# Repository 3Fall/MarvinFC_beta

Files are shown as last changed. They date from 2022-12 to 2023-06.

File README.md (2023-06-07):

# Marvin - the [soon] ultimate open-source rocket flight computer
### Suitable for middle to high power rockets.

>  - Hey, let's take whatever's left of our energy to live, and jam it into another flight computer, 
but this time let's make it posh and fix all the issues of the previous designs.
>  - No.
>  - We can use some pogo pin connectors.
>  - Fine.

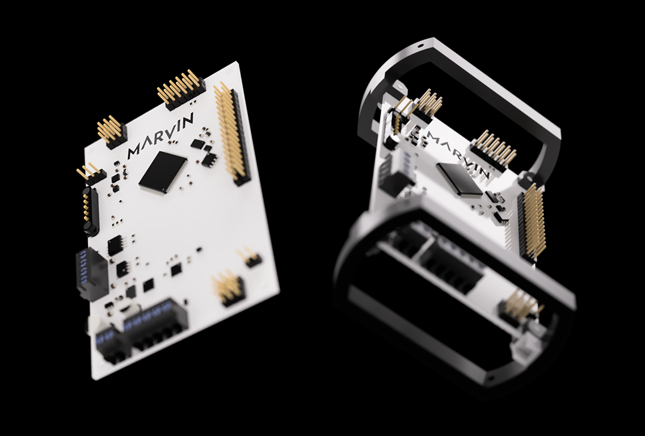
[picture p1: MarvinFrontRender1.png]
MarvinPic


# Specs:
- 65x100mm 1.6mm thick PCB
- 168Mhz STM32F407
- Separate power management chip ATTINY1607
- 3.3V, 5VPower, 5VExtension power buses
- Dual high current pyro channels with continuity detection circuitry
- 6 PWM outputs
- LSM6DSOTR IMU in sensor fusion configuration with LIS3MDLTR magnetometer
- MS5611 pressure sensor, barometric altitude and BMP280 as a redundancy or the budget friendly option
- Data logging to a 16Mbit flash memory chip and/or micro SD card
- 32 free GPIO
- Short time of black box data logging after an unexpected power outage 
- The coolest debug connector ever
- Default 433Mhz Ra-02 radio module (with proper antenna > 4km open space range easily achievable)
- Status and power indication LEDs

## Marvin is currently in testing phase, the schematics will likely change, but the development happens on our private server. Here, every version that gets put into production will be published.

# V2 Release:
- changed the magnetometer connection (now it's interfaced with the MCU directly)
- changed micro SD slot to one with visible pins
- fixed the lacking IMU I2C address pin connection (it was left floating in V1)
- the BMP280 pads were scaled up a bit, previously small enough to cause manufacturing problems with JLCPCB
- added power pins among the expansion pin deck
- added thermal relief to ground planes
- fixed the debug UART RX and TX labels
- added a buzzer
- added JST connectors for 3 of 6 PWM channels
- fixed the power management IC footprint
- changed the mounting holes to M3
- changed one of the LDO IC's to a different part

DevelopmentPic

Designed to fly a TVC rocket guided by artificial intelligence.
All the schematics and PCB files are available in the repo, but Marvin hasn't flown yet. Once it becomes flight proven, official version will be released.

# Software

```
The software is application specific, and thus not public.
```
Although below is the System Manager Firmware for the advanced power supply functionality.
> https://github.com/3Fall/Marvin_SystemManager_Firmware

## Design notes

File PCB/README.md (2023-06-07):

# marvin_v2

## TODO:

| What | Status | Notes
|---|---|---|
|Switch to 0805 footprints | ✅ | we too lazy |
|Magnetometer to mcu directly (no fusion config) | ✅ | done |
|AP622 swap | ✅ | we dont swap ig? |
|SD SLOT to one with visible pins | ✅ | done |
|IMU address pin | ✅ | done |
|Bigger bmp pads | ✅ | done |
|Voltage pins among PA and PE rows | ✅ | done |
|Sma for radio | ✅ | y tho |
| Add thermal relief to ground plane(s) | ✅ | DONE |
| Debug uart rx tx labels | ✅ | Switched around according to mcu docs |
|Buzzer | ✅ | added |
|Quick-plug connector | ✅ | added |
|Jst servo connectors | ✅ | added |
|PAC footprint | ✅ | switched |
|Mounting holes to m3 | ✅ | changed |
| U6 LDO swap | ✅ | chnged |

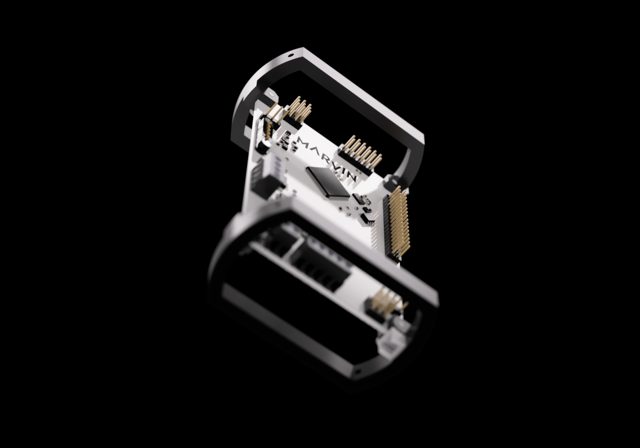
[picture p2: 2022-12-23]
Marvin1BackMount2.png

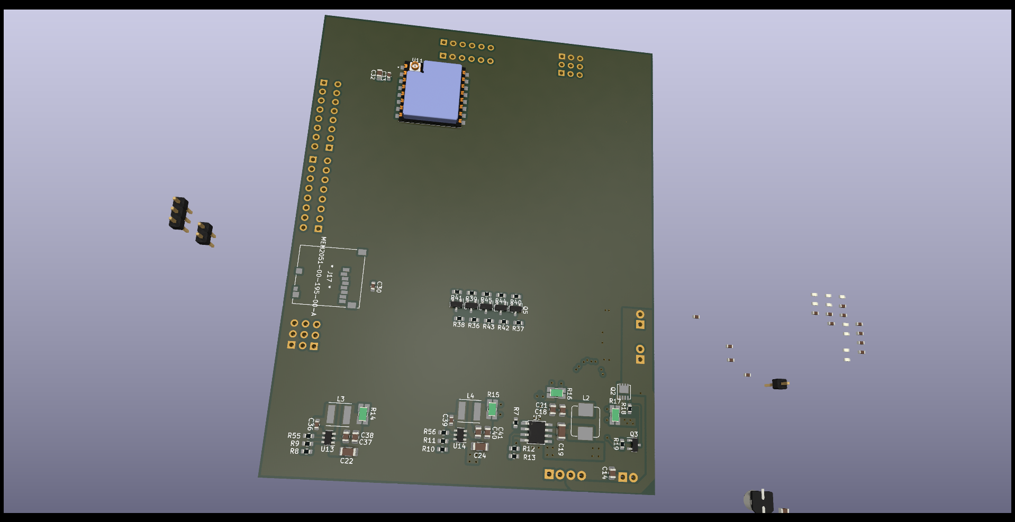
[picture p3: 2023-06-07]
PCB/marvin_fc_board.png

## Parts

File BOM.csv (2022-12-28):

Date: | 12/28/2022 5:08:15 PM
Tool: | Eeschema (6.0.10)
Component Count: | 160
Individual Components:
Item | Qty | Reference(s) | Value | LibPart | Footprint | Datasheet | MANUFACTURER | MAXIMUM_PACKAGE_HEIGHT | PARTREV | STANDARD
 |  | C1 | 20pF | Device:C_Small | Capacitor_SMD:C_0603_1608Metric | ~
 |  | C2 | 20pF | Device:C_Small | Capacitor_SMD:C_0603_1608Metric | ~
 |  | C3 | 100nF | Device:C_Small | Capacitor_SMD:C_0603_1608Metric | ~
 |  | C4 | 1uF | Device:C_Small | Capacitor_SMD:C_0603_1608Metric | ~
 |  | C5 | 2.2uF | Device:C_Small | Capacitor_SMD:C_0603_1608Metric | ~
 |  | C6 | 2.2uF | Device:C_Small | Capacitor_SMD:C_0603_1608Metric | ~
 |  | C7 | 1uF | Device:C_Small | Capacitor_SMD:C_0603_1608Metric | ~
 |  | C8 | 100nF | Device:C_Small | Capacitor_SMD:C_0603_1608Metric | ~
 |  | C9 | 100nF | Device:C_Small | Capacitor_SMD:C_0603_1608Metric | ~
 |  | C10 | 100nF | Device:C_Small | Capacitor_SMD:C_0603_1608Metric | ~
 |  | C11 | 1uF | Device:C_Small | Capacitor_SMD:C_0603_1608Metric | ~
 |  | C12 | 100nF | Device:C_Small | Capacitor_SMD:C_0603_1608Metric | ~
 |  | C13 | 100nF | Device:C_Small | Capacitor_SMD:C_0603_1608Metric | ~
 |  | C14 | 100nF | Device:C_Small | Capacitor_SMD:C_0603_1608Metric | ~
 |  | C15 | 100nF | Device:C_Small | Capacitor_SMD:C_0603_1608Metric | ~
 |  | C16 | 10u | Device:C | Capacitor_SMD:C_0805_2012Metric | ~
 |  | C17 | 10u | Device:C | Capacitor_SMD:C_0603_1608Metric | ~
 |  | C18 | 1000u | Device:C_Polarized | Capacitor_SMD:CP_Elec_6.3x7.7 | ~
 |  | C19 | 3300u | Device:C_Polarized | Capacitor_SMD:CP_Elec_5x5.4 | ~
 |  | C20 | 22u | Device:C | Capacitor_SMD:C_0805_2012Metric | ~
 |  | C21 | 10u | Device:C | Capacitor_SMD:C_1206_3216Metric | ~
 |  | C22 | 100n | Device:C | Capacitor_SMD:C_0603_1608Metric | ~
 |  | C23 | 22u | Device:C | Capacitor_SMD:C_0805_2012Metric | ~
 |  | C24 | 10u | Device:C | Capacitor_SMD:C_1206_3216Metric | ~
 |  | C25 | 100n | Device:C | Capacitor_SMD:C_0603_1608Metric | ~
 |  | C26 | 10u | Device:C | Capacitor_SMD:C_1206_3216Metric | ~
 |  | C27 | 100n | Device:C | Capacitor_SMD:C_0603_1608Metric | ~
 |  | C28 | 10u | Device:C | Capacitor_SMD:C_0805_2012Metric | ~
 |  | C29 | 100n | Device:C | Capacitor_SMD:C_0603_1608Metric | ~
 |  | C30 | 100n | Device:C | Capacitor_SMD:C_0603_1608Metric | ~
 |  | C31 | C | Device:C | Capacitor_SMD:C_0603_1608Metric | ~
 |  | C32 | 100n | Device:C | Capacitor_SMD:C_0603_1608Metric | ~
 |  | C33 | C | Device:C | Capacitor_SMD:C_0603_1608Metric | ~
 |  | C34 | 100nF | Device:C_Small | Capacitor_SMD:C_0603_1608Metric | ~
 |  | C35 | 100nF | Device:C_Small | Capacitor_SMD:C_0603_1608Metric | ~
 |  | C36 | 10u | Device:C | Capacitor_SMD:C_0805_2012Metric | ~
 |  | C37 | 100n | Device:C | Capacitor_SMD:C_0603_1608Metric | ~
 |  | C38 | 100u | Device:C | Capacitor_SMD:C_0805_2012Metric | ~
 |  | C39 | 100u | Device:C | Capacitor_SMD:C_0805_2012Metric | ~
 |  | C40 | 100n | Device:C_Small | Capacitor_SMD:C_0603_1608Metric | ~
 |  | C41 | 22u | Device:C | Capacitor_SMD:C_0805_2012Metric | ~
 |  | C42 | 22u | Device:C | Capacitor_SMD:C_0805_2012Metric | ~
 |  | C43 | 100n | Device:C_Small | Capacitor_SMD:C_0603_1608Metric | ~
 |  | C44 | 22u | Device:C | Capacitor_SMD:C_0805_2012Metric | ~
 |  | C45 | 22u | Device:C | Capacitor_SMD:C_0805_2012Metric | ~
 |  | D1 | LED_RGBK | Device:LED_RGBK | LED_SMD:LED_Cree-PLCC4_2x2mm_CW | ~
 |  | D2 | CUS08F30 | Device:D_Schottky | Diode_SMD:D_SOD-323_HandSoldering | ~
 |  | D3 | VBAT | Device:LED | LED_SMD:LED_0603_1608Metric_Pad1.05x0.95mm_HandSolder | ~
 |  | D4 | V5L | Device:LED | LED_SMD:LED_0603_1608Metric_Pad1.05x0.95mm_HandSolder | ~
 |  | D5 | V5P | Device:LED | LED_SMD:LED_0603_1608Metric_Pad1.05x0.95mm_HandSolder | ~
 |  | D6 | 3V3 | Device:LED | LED_SMD:LED_0603_1608Metric_Pad1.05x0.95mm_HandSolder | ~
 |  | D7 | LED_RGBK | Device:LED_RGBK | LED_SMD:LED_Cree-PLCC4_2x2mm_CW | ~
 |  | F1 | 200mA | Device:Polyfuse_Small | Fuse:Fuse_0603_1608Metric | ~
 |  | F2 | 200mA | Device:Polyfuse_Small | Fuse:Fuse_0603_1608Metric | ~
 |  | FB1 | FerriteBead | Device:FerriteBead | Inductor_SMD:L_0805_2012Metric | ~
 |  | FB2 | FerriteBead | Device:FerriteBead | Inductor_SMD:L_0805_2012Metric | ~
 |  | J1 | PROG / DBG | Connector_Generic:Conn_01x06 | Connector_PinHeader_2.54mm:PinHeader_1x06_P2.54mm_Vertical | ~
 |  | J2 | EXPA | Connector_Generic:Conn_01x08 | Connector_PinHeader_2.54mm:PinHeader_1x08_P2.54mm_Vertical | ~
 |  | J3 | EXPC | Connector_Generic:Conn_01x08 | Connector_PinHeader_2.54mm:PinHeader_1x08_P2.54mm_Vertical | ~
 |  | J4 | SERVO POW 1 | Connector_Generic:Conn_02x03_Odd_Even | Connector_PinHeader_2.54mm:PinHeader_2x03_P2.54mm_Vertical | ~
 |  | J5 | SERVO POW 2 | Connector_Generic:Conn_02x03_Odd_Even | Connector_PinHeader_2.54mm:PinHeader_2x03_P2.54mm_Vertical | ~
 |  | J6 | EXPB | Connector_Generic:Conn_01x08 | Connector_PinHeader_2.54mm:PinHeader_1x08_P2.54mm_Vertical | ~
 |  | J7 | EXPD | Connector_Generic:Conn_01x08 | Connector_PinHeader_2.54mm:PinHeader_1x08_P2.54mm_Vertical | ~
 |  | J8 | SERVO SIG 1 | Connector_Generic:Conn_01x03 | Connector_PinHeader_2.54mm:PinHeader_1x03_P2.54mm_Vertical | ~
 |  | J9 | SERVO SIG 2 | Connector_Generic:Conn_01x03 | Connector_PinHeader_2.54mm:PinHeader_1x03_P2.54mm_Vertical | ~
 |  | J10 | EXP1 | Connector_Generic:Conn_01x06 | Connector_PinHeader_2.54mm:PinHeader_1x06_P2.54mm_Vertical | ~
 |  | J11 | EXP2 | Connector_Generic:Conn_01x06 | Connector_PinHeader_2.54mm:PinHeader_1x06_P2.54mm_Vertical | ~
 |  | J12 | POWER_IN | Connector:Screw_Terminal_01x02 | TerminalBlock_4Ucon:TerminalBlock_4Ucon_1x02_P3.50mm_Vertical | ~
 |  | J13 | EXTl NTC | Connector_Generic:Conn_01x02 | Connector_PinHeader_2.54mm:PinHeader_1x02_P2.54mm_Vertical | ~
 |  | J14 | Screw_Terminal_01x05 | Connector:Screw_Terminal_01x05 | TerminalBlock_4Ucon:TerminalBlock_4Ucon_1x05_P3.50mm_Vertical | ~
 |  | J15 | ATTINY_DBG | Connector_Generic:Conn_01x03 | Connector_PinHeader_2.54mm:PinHeader_1x03_P2.54mm_Vertical | ~
 |  | J16 | MEM2051-00-195-00-A | MEM:MEM2051-00-195-00-A | SD:MEM2051-00-195-00-A
 |  | J17 | Pyro Terminal 1 | Connector:Screw_Terminal_01x02 | TerminalBlock_4Ucon:TerminalBlock_4Ucon_1x02_P3.50mm_Vertical | ~
 |  | J18 | Pyro Terminal 2 | Connector:Screw_Terminal_01x02 | TerminalBlock_4Ucon:TerminalBlock_4Ucon_1x02_P3.50mm_Vertical | ~
 |  | JP1 | SB_B | Jumper:SolderJumper_2_Bridged | Jumper:SolderJumper-2_P1.3mm_Bridged_Pad1.0x1.5mm | ~
 |  | JP2 | SB_B | Jumper:SolderJumper_2_Bridged | Jumper:SolderJumper-2_P1.3mm_Bridged_Pad1.0x1.5mm | ~
 |  | JP3 | SB C | Jumper:SolderJumper_2_Bridged | Jumper:SolderJumper-2_P1.3mm_Bridged_Pad1.0x1.5mm | ~
 |  | JP4 | SB O | Jumper:SolderJumper_2_Open | Jumper:SolderJumper-2_P1.3mm_Open_Pad1.0x1.5mm | ~
 |  | JP5 | SB O | Jumper:SolderJumper_2_Open | Jumper:SolderJumper-2_P1.3mm_Open_Pad1.0x1.5mm | ~
 |  | JP6 | SB C | Jumper:SolderJumper_2_Bridged | Jumper:SolderJumper-2_P1.3mm_Bridged_Pad1.0x1.5mm | ~
 |  | JP7 | SB O | Jumper:SolderJumper_2_Open | Jumper:SolderJumper-2_P1.3mm_Open_Pad1.0x1.5mm | ~
 |  | L1 | L_Ferrite | Device:L_Ferrite | Inductor_SMD:L_0805_2012Metric | ~
 |  | L2 | 3u3 | Device:L_Ferrite | Inductor_SMD:L_Bourns_SRP7028A_7.3x6.6mm | ~
 |  | L3 | 4,7u | Device:L_Ferrite | Inductor_SMD:L_Taiyo-Yuden_NR-50xx | ~
 |  | L4 | 4,7u | Device:L_Ferrite | Inductor_SMD:L_Taiyo-Yuden_NR-50xx | ~
 |  | Q1 | SISH101DN | Transistor_FET:SiS415DNT | Package_SO:Vishay_PowerPAK_1212-8_Single | https://www.vishay.com/docs/63684/sis415dnt.pdf
 |  | Q2 | SISH101DN | Transistor_FET:SiS415DNT | Package_SO:Vishay_PowerPAK_1212-8_Single | https://www.vishay.com/docs/63684/sis415dnt.pdf
 |  | Q3 | BC847 | Transistor_BJT:BC847 | Package_TO_SOT_SMD:SOT-23 | http://www.infineon.com/dgdl/Infineon-BC847SERIES_BC848SERIES_BC849SERIES_BC850SERIES-DS-v01_01-en.pdf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
 |  | Q4 | AO4822A | Transistor_FET:FDS6890A | Package_SO:SOIC-8_3.9x4.9mm_P1.27mm | https://www.onsemi.com/pub/Collateral/FDS6890A-D.PDF
 |  | R1 | 510ohm | Device:R | Resistor_SMD:R_0603_1608Metric | ~
 |  | R2 | 0 Ohm | Device:R | Resistor_SMD:R_0603_1608Metric | ~
 |  | R3 | NC | Device:R | Resistor_SMD:R_0603_1608Metric | ~
 |  | R4 | 46ohm | Device:R | Resistor_SMD:R_0603_1608Metric | ~
 |  | R5 | 330 | Device:R | Resistor_SMD:R_0603_1608Metric | ~
 |  | R6 | NC | Device:R | Resistor_SMD:R_0603_1608Metric | ~
 |  | R7 | NC | Device:R | Resistor_SMD:R_0603_1608Metric | ~
 |  | R8 | NC | Device:R | Resistor_SMD:R_0603_1608Metric | ~
 |  | R9 | 10k | Device:R | Resistor_SMD:R_0603_1608Metric | ~
 |  | R10 | 2137 | Device:R | Resistor_SMD:R_0603_1608Metric | ~
 |  | R11 | 42069 | Device:R | Resistor_SMD:R_0603_1608Metric | ~
 |  | R12 | ? | Device:R | Resistor_SMD:R_0603_1608Metric | ~
 |  | R13 | ? | Device:R | Resistor_SMD:R_0603_1608Metric | ~
 |  | R14 | 2137 | Device:R | Resistor_SMD:R_0603_1608Metric | ~
 |  | R15 | R | Device:R | Resistor_SMD:R_0603_1608Metric | ~
 |  | R16 | 0.05 | Device:R_Shunt | Resistor_SMD:R_Shunt_Ohmite_LVK12 | ~
 |  | R17 | 0.05 | Device:R_Shunt | Resistor_SMD:R_Shunt_Ohmite_LVK12 | ~
 |  | R18 | 0.01 | Device:R_Shunt | Resistor_SMD:R_Shunt_Ohmite_LVK12 | ~
 |  | R19 | 0.01 | Device:R_Shunt | Resistor_SMD:R_Shunt_Ohmite_LVK12 | ~
 |  | R20 | 10k | Device:R | Resistor_SMD:R_0603_1608Metric | ~
 |  | R21 | 10k | Device:R | Resistor_SMD:R_0603_1608Metric | ~
 |  | R22 | 10k | Device:R | Resistor_SMD:R_0603_1608Metric | ~
 |  | R23 | 4.7k | Device:R | Resistor_SMD:R_0603_1608Metric | ~
 |  | R24 | 10k | Device:R | Resistor_SMD:R_0603_1608Metric | ~
 |  | R25 | 10k | Device:R | Resistor_SMD:R_0603_1608Metric | ~
 |  | R26 | 2k | Device:R | Resistor_SMD:R_0603_1608Metric | ~
 |  | R27 | 500 | Device:R | Resistor_SMD:R_0603_1608Metric | ~
 |  | R28 | 2k | Device:R | Resistor_SMD:R_0603_1608Metric | ~
 |  | R29 | 500 | Device:R | Resistor_SMD:R_0603_1608Metric | ~
 |  | R30 | 500 | Device:R | Resistor_SMD:R_0603_1608Metric | ~
 |  | R31 | 500 | Device:R | Resistor_SMD:R_0603_1608Metric | ~
 |  | R32 | 300 | Device:R | Resistor_SMD:R_0603_1608Metric | ~
 |  | R33 | R | Device:R | Resistor_SMD:R_0603_1608Metric | ~
 |  | R34 | 2k | Device:R | Resistor_SMD:R_0603_1608Metric | ~
 |  | R35 | 2k | Device:R | Resistor_SMD:R_0603_1608Metric | ~
 |  | R36 | R | Device:R | Resistor_SMD:R_0603_1608Metric | ~
 |  | R37 | 2k | Device:R | Resistor_SMD:R_0603_1608Metric | ~
 |  | R38 | 2k | Device:R | Resistor_SMD:R_0603_1608Metric | ~
 |  | R39 | 10k | Device:R | Resistor_SMD:R_0603_1608Metric | ~
 |  | R40 | 370 | Device:R | Resistor_SMD:R_0603_1608Metric | ~
 |  | R41 | 1k | Device:R | Resistor_SMD:R_0603_1608Metric | ~
 |  | R42 | 10k | Device:R | Resistor_SMD:R_0603_1608Metric | ~
 |  | R43 | 370 | Device:R | Resistor_SMD:R_0603_1608Metric | ~
 |  | R44 | 1k | Device:R | Resistor_SMD:R_0603_1608Metric | ~
 |  | R45 | 10k | Device:R | Resistor_SMD:R_0603_1608Metric | ~
 |  | R46 | 10k | Device:R | Resistor_SMD:R_0603_1608Metric | ~
 |  | SW1 | SW_Push | Switch:SW_Push | FancySwitch:FancySwitchFootprint | ~
 |  | SW2 | SW_Push | Switch:SW_Push | FancySwitch:FancySwitchFootprint | ~
 |  | SW3 | SW_Push | Switch:SW_Push | FancySwitch:FancySwitchFootprint | ~
 |  | TP1 | 5V_BOOT | Connector:TestPoint | TestPoint:TestPoint_Pad_D1.5mm | ~
 |  | TP2 | VBUS | Connector:TestPoint | TestPoint:TestPoint_Pad_D1.5mm | ~
 |  | TP3 | VBAT | Connector:TestPoint | TestPoint:TestPoint_Pad_D1.5mm | ~
 |  | U1 | STM32F407 | MCU_ST_STM32F4:STM32F407VGTx | Package_QFP:LQFP-100_14x14mm_P0.5mm | http://www.st.com/st-web-ui/static/active/en/resource/technical/document/datasheet/DM00037051.pdf
 |  | U2 | BMP280 | Sensor_Pressure:BMP280 | Package_LGA:Bosch_LGA-8_2x2.5mm_P0.65mm_ClockwisePinNumbering | https://ae-bst.resource.bosch.com/media/_tech/media/datasheets/BST-BMP280-DS001.pdf
 |  | U3 | LSM6DSOTR | LSMDSO:LSM6DSOTR | Package_LGA:LGA-14_3x2.5mm_P0.5mm_LayoutBorder3x4y
 |  | U4 | LIS3MDLTR | LIS3:LIS3MDLTR | Package_LGA:LGA-12_2x2mm_P0.5mm
 |  | U5 | MS5611-01BA | Sensor_Pressure:MS5611-01BA | Package_LGA:LGA-8_3x5mm_P1.25mm | https://www.te.com/commerce/DocumentDelivery/DDEController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
 |  | U6 | NCP718xSN500 | Regulator_Linear:NCP718xSN500 | Package_TO_SOT_SMD:SOT-23-5 | https://www.onsemi.com/pub/Collateral/NCP718-D.PDF
 |  | U7 | ST1S41PHR | Regulator_Switching:ST1S10PHR | Package_SO:TI_SO-PowerPAD-8 | http://www.st.com/internet/com/TECHNICAL_RESOURCES/TECHNICAL_LITERATURE/DATASHEET/CD00169322.pdf
 |  | U8 | PAC1954 | Analog_ADC:PAC1934x-xJQ | Package_DFN_QFN:UQFN-16-1EP_4x4mm_P0.65mm_EP2.7x2.7mm | http://ww1.microchip.com/downloads/en/DeviceDoc/PAC1931-Family-Data-Sheet-DS20005850E.pdf
 |  | U9 | ATtiny1627-M | MCU_Microchip_ATtiny:ATtiny827-M | Package_DFN_QFN:QFN-24-1EP_4x4mm_P0.5mm_EP2.6x2.6mm | https://ww1.microchip.com/downloads/en/DeviceDoc/ATtiny424-426-427-824-826-827-DataSheet-DS40002311A.pdf
 |  | U10 | TXB0108DQSR | Logic_LevelTranslator:TXB0108DQSR | TXB0108:IC_TXB0108RGYR | http://www.ti.com/lit/ds/symlink/txb0108.pdf
 |  | U11 | W25Q16JLSSIG | W25Q:W25Q16JLSSIG | Package_SO:SOIC-8_3.9x4.9mm_P1.27mm
 |  | U12 | RA-02_LORA | RA 02:RA-02_LORA | LORA:MODULE_RA-02_LORA |  | Ai-Thinker | 3.3mm | 2018/03/02 | Manufacturer Recommendations
 |  | U13 | ILD213T | Isolator:LTV-827 | Package_SO:SO-8_5.3x6.2mm_P1.27mm | http://optoelectronics.liteon.com/upload/download/DS-70-96-0016/LTV-8X7%20series%20201610%20.pdf
 |  | U14 | AP62200Z6 | Regulator_Switching:AP62250Z6 | Package_SO:TSOP-6_1.65x3.05mm_P0.95mm | https://www.diodes.com/assets/Datasheets/AP62250.pdf
 |  | U15 | AP62200Z6 | Regulator_Switching:AP62250Z6 | Package_SO:TSOP-6_1.65x3.05mm_P0.95mm | https://www.diodes.com/assets/Datasheets/AP62250.pdf
 |  | U16 | MCP9700AT-ELT | Sensor_Temperature:MCP9700AT-ELT | Package_TO_SOT_SMD:SOT-353_SC-70-5 | http://ww1.microchip.com/downloads/en/DeviceDoc/20001942G.pdf
 |  | U17 | MCP9700AT-ELT | Sensor_Temperature:MCP9700AT-ELT | Package_TO_SOT_SMD:SOT-353_SC-70-5 | http://ww1.microchip.com/downloads/en/DeviceDoc/20001942G.pdf
 |  | U18 | MCP9700AT-ELT | Sensor_Temperature:MCP9700AT-ELT | Package_TO_SOT_SMD:SOT-353_SC-70-5 | http://ww1.microchip.com/downloads/en/DeviceDoc/20001942G.pdf
 |  | Y1 | Crystal_GND24 | Device:Crystal_GND24 | Oscillator:Oscillator_SMD_SeikoEpson_SG210-4Pin_2.5x2.0mm | ~
Collated Components:
Item | Qty | Reference(s) | Value | LibPart | Footprint | Datasheet | MANUFACTURER | MAXIMUM_PACKAGE_HEIGHT | PARTREV | STANDARD
1 | 2 | C1, C2 | 20pF | Device:C_Small | Capacitor_SMD:C_0603_1608Metric | ~
2 | 10 | C3, C8, C9, C10, C12, C13, C14, C15, C34, C35 | 100nF | Device:C_Small | Capacitor_SMD:C_0603_1608Metric | ~
3 | 3 | C4, C7, C11 | 1uF | Device:C_Small | Capacitor_SMD:C_0603_1608Metric | ~
4 | 2 | C5, C6 | 2.2uF | Device:C_Small | Capacitor_SMD:C_0603_1608Metric | ~
5 | 3 | C16, C28, C36 | 10u | Device:C | Capacitor_SMD:C_0805_2012Metric | ~
6 | 1 | C17 | 10u | Device:C | Capacitor_SMD:C_0603_1608Metric | ~
7 | 1 | C18 | 1000u | Device:C_Polarized | Capacitor_SMD:CP_Elec_6.3x7.7 | ~
8 | 1 | C19 | 3300u | Device:C_Polarized | Capacitor_SMD:CP_Elec_5x5.4 | ~
9 | 6 | C20, C23, C41, C42, C44, C45 | 22u | Device:C | Capacitor_SMD:C_0805_2012Metric | ~
10 | 3 | C21, C24, C26 | 10u | Device:C | Capacitor_SMD:C_1206_3216Metric | ~
11 | 7 | C22, C25, C27, C29, C30, C32, C37 | 100n | Device:C | Capacitor_SMD:C_0603_1608Metric | ~
12 | 2 | C31, C33 | C | Device:C | Capacitor_SMD:C_0603_1608Metric | ~
13 | 2 | C38, C39 | 100u | Device:C | Capacitor_SMD:C_0805_2012Metric | ~
14 | 2 | C40, C43 | 100n | Device:C_Small | Capacitor_SMD:C_0603_1608Metric | ~
15 | 2 | D1, D7 | LED_RGBK | Device:LED_RGBK | LED_SMD:LED_Cree-PLCC4_2x2mm_CW | ~
16 | 1 | D2 | CUS08F30 | Device:D_Schottky | Diode_SMD:D_SOD-323_HandSoldering | ~
17 | 1 | D3 | VBAT | Device:LED | LED_SMD:LED_0603_1608Metric_Pad1.05x0.95mm_HandSolder | ~
18 | 1 | D4 | V5L | Device:LED | LED_SMD:LED_0603_1608Metric_Pad1.05x0.95mm_HandSolder | ~
19 | 1 | D5 | V5P | Device:LED | LED_SMD:LED_0603_1608Metric_Pad1.05x0.95mm_HandSolder | ~
20 | 1 | D6 | 3V3 | Device:LED | LED_SMD:LED_0603_1608Metric_Pad1.05x0.95mm_HandSolder | ~
21 | 2 | F1, F2 | 200mA | Device:Polyfuse_Small | Fuse:Fuse_0603_1608Metric | ~
22 | 2 | FB1, FB2 | FerriteBead | Device:FerriteBead | Inductor_SMD:L_0805_2012Metric | ~
23 | 1 | J1 | PROG / DBG | Connector_Generic:Conn_01x06 | Connector_PinHeader_2.54mm:PinHeader_1x06_P2.54mm_Vertical | ~
24 | 1 | J2 | EXPA | Connector_Generic:Conn_01x08 | Connector_PinHeader_2.54mm:PinHeader_1x08_P2.54mm_Vertical | ~
25 | 1 | J3 | EXPC | Connector_Generic:Conn_01x08 | Connector_PinHeader_2.54mm:PinHeader_1x08_P2.54mm_Vertical | ~
26 | 1 | J4 | SERVO POW 1 | Connector_Generic:Conn_02x03_Odd_Even | Connector_PinHeader_2.54mm:PinHeader_2x03_P2.54mm_Vertical | ~
27 | 1 | J5 | SERVO POW 2 | Connector_Generic:Conn_02x03_Odd_Even | Connector_PinHeader_2.54mm:PinHeader_2x03_P2.54mm_Vertical | ~
28 | 1 | J6 | EXPB | Connector_Generic:Conn_01x08 | Connector_PinHeader_2.54mm:PinHeader_1x08_P2.54mm_Vertical | ~
29 | 1 | J7 | EXPD | Connector_Generic:Conn_01x08 | Connector_PinHeader_2.54mm:PinHeader_1x08_P2.54mm_Vertical | ~
30 | 1 | J8 | SERVO SIG 1 | Connector_Generic:Conn_01x03 | Connector_PinHeader_2.54mm:PinHeader_1x03_P2.54mm_Vertical | ~
31 | 1 | J9 | SERVO SIG 2 | Connector_Generic:Conn_01x03 | Connector_PinHeader_2.54mm:PinHeader_1x03_P2.54mm_Vertical | ~
32 | 1 | J10 | EXP1 | Connector_Generic:Conn_01x06 | Connector_PinHeader_2.54mm:PinHeader_1x06_P2.54mm_Vertical | ~
33 | 1 | J11 | EXP2 | Connector_Generic:Conn_01x06 | Connector_PinHeader_2.54mm:PinHeader_1x06_P2.54mm_Vertical | ~
34 | 1 | J12 | POWER_IN | Connector:Screw_Terminal_01x02 | TerminalBlock_4Ucon:TerminalBlock_4Ucon_1x02_P3.50mm_Vertical | ~
35 | 1 | J13 | EXTl NTC | Connector_Generic:Conn_01x02 | Connector_PinHeader_2.54mm:PinHeader_1x02_P2.54mm_Vertical | ~
36 | 1 | J14 | Screw_Terminal_01x05 | Connector:Screw_Terminal_01x05 | TerminalBlock_4Ucon:TerminalBlock_4Ucon_1x05_P3.50mm_Vertical | ~
37 | 1 | J15 | ATTINY_DBG | Connector_Generic:Conn_01x03 | Connector_PinHeader_2.54mm:PinHeader_1x03_P2.54mm_Vertical | ~
38 | 1 | J16 | MEM2051-00-195-00-A | MEM:MEM2051-00-195-00-A | SD:MEM2051-00-195-00-A
39 | 1 | J17 | Pyro Terminal 1 | Connector:Screw_Terminal_01x02 | TerminalBlock_4Ucon:TerminalBlock_4Ucon_1x02_P3.50mm_Vertical | ~
40 | 1 | J18 | Pyro Terminal 2 | Connector:Screw_Terminal_01x02 | TerminalBlock_4Ucon:TerminalBlock_4Ucon_1x02_P3.50mm_Vertical | ~
41 | 2 | JP1, JP2 | SB_B | Jumper:SolderJumper_2_Bridged | Jumper:SolderJumper-2_P1.3mm_Bridged_Pad1.0x1.5mm | ~
42 | 2 | JP3, JP6 | SB C | Jumper:SolderJumper_2_Bridged | Jumper:SolderJumper-2_P1.3mm_Bridged_Pad1.0x1.5mm | ~
43 | 3 | JP4, JP5, JP7 | SB O | Jumper:SolderJumper_2_Open | Jumper:SolderJumper-2_P1.3mm_Open_Pad1.0x1.5mm | ~
44 | 1 | L1 | L_Ferrite | Device:L_Ferrite | Inductor_SMD:L_0805_2012Metric | ~
45 | 1 | L2 | 3u3 | Device:L_Ferrite | Inductor_SMD:L_Bourns_SRP7028A_7.3x6.6mm | ~
46 | 2 | L3, L4 | 4,7u | Device:L_Ferrite | Inductor_SMD:L_Taiyo-Yuden_NR-50xx | ~
47 | 2 | Q1, Q2 | SISH101DN | Transistor_FET:SiS415DNT | Package_SO:Vishay_PowerPAK_1212-8_Single | https://www.vishay.com/docs/63684/sis415dnt.pdf
48 | 1 | Q3 | BC847 | Transistor_BJT:BC847 | Package_TO_SOT_SMD:SOT-23 | http://www.infineon.com/dgdl/Infineon-BC847SERIES_BC848SERIES_BC849SERIES_BC850SERIES-DS-v01_01-en.pdf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
49 | 1 | Q4 | AO4822A | Transistor_FET:FDS6890A | Package_SO:SOIC-8_3.9x4.9mm_P1.27mm | https://www.onsemi.com/pub/Collateral/FDS6890A-D.PDF
50 | 1 | R1 | 510ohm | Device:R | Resistor_SMD:R_0603_1608Metric | ~
51 | 1 | R2 | 0 Ohm | Device:R | Resistor_SMD:R_0603_1608Metric | ~
52 | 4 | R3, R6, R7, R8 | NC | Device:R | Resistor_SMD:R_0603_1608Metric | ~
53 | 1 | R4 | 46ohm | Device:R | Resistor_SMD:R_0603_1608Metric | ~
54 | 1 | R5 | 330 | Device:R | Resistor_SMD:R_0603_1608Metric | ~
55 | 10 | R9, R20, R21, R22, R24, R25, R39, R42, R45, R46 | 10k | Device:R | Resistor_SMD:R_0603_1608Metric | ~
56 | 2 | R10, R14 | 2137 | Device:R | Resistor_SMD:R_0603_1608Metric | ~
57 | 1 | R11 | 42069 | Device:R | Resistor_SMD:R_0603_1608Metric | ~
58 | 2 | R12, R13 | ? | Device:R | Resistor_SMD:R_0603_1608Metric | ~
59 | 3 | R15, R33, R36 | R | Device:R | Resistor_SMD:R_0603_1608Metric | ~
60 | 2 | R16, R17 | 0.05 | Device:R_Shunt | Resistor_SMD:R_Shunt_Ohmite_LVK12 | ~
61 | 2 | R18, R19 | 0.01 | Device:R_Shunt | Resistor_SMD:R_Shunt_Ohmite_LVK12 | ~
62 | 1 | R23 | 4.7k | Device:R | Resistor_SMD:R_0603_1608Metric | ~
63 | 6 | R26, R28, R34, R35, R37, R38 | 2k | Device:R | Resistor_SMD:R_0603_1608Metric | ~
64 | 4 | R27, R29, R30, R31 | 500 | Device:R | Resistor_SMD:R_0603_1608Metric | ~
65 | 1 | R32 | 300 | Device:R | Resistor_SMD:R_0603_1608Metric | ~
66 | 2 | R40, R43 | 370 | Device:R | Resistor_SMD:R_0603_1608Metric | ~
67 | 2 | R41, R44 | 1k | Device:R | Resistor_SMD:R_0603_1608Metric | ~
68 | 3 | SW1, SW2, SW3 | SW_Push | Switch:SW_Push | FancySwitch:FancySwitchFootprint | ~
69 | 1 | TP1 | 5V_BOOT | Connector:TestPoint | TestPoint:TestPoint_Pad_D1.5mm | ~
70 | 1 | TP2 | VBUS | Connector:TestPoint | TestPoint:TestPoint_Pad_D1.5mm | ~
71 | 1 | TP3 | VBAT | Connector:TestPoint | TestPoint:TestPoint_Pad_D1.5mm | ~
72 | 1 | U1 | STM32F407 | MCU_ST_STM32F4:STM32F407VGTx | Package_QFP:LQFP-100_14x14mm_P0.5mm | http://www.st.com/st-web-ui/static/active/en/resource/technical/document/datasheet/DM00037051.pdf
73 | 1 | U2 | BMP280 | Sensor_Pressure:BMP280 | Package_LGA:Bosch_LGA-8_2x2.5mm_P0.65mm_ClockwisePinNumbering | https://ae-bst.resource.bosch.com/media/_tech/media/datasheets/BST-BMP280-DS001.pdf
74 | 1 | U3 | LSM6DSOTR | LSMDSO:LSM6DSOTR | Package_LGA:LGA-14_3x2.5mm_P0.5mm_LayoutBorder3x4y
75 | 1 | U4 | LIS3MDLTR | LIS3:LIS3MDLTR | Package_LGA:LGA-12_2x2mm_P0.5mm
76 | 1 | U5 | MS5611-01BA | Sensor_Pressure:MS5611-01BA | Package_LGA:LGA-8_3x5mm_P1.25mm | https://www.te.com/commerce/DocumentDelivery/DDEController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
77 | 1 | U6 | NCP718xSN500 | Regulator_Linear:NCP718xSN500 | Package_TO_SOT_SMD:SOT-23-5 | https://www.onsemi.com/pub/Collateral/NCP718-D.PDF
78 | 1 | U7 | ST1S41PHR | Regulator_Switching:ST1S10PHR | Package_SO:TI_SO-PowerPAD-8 | http://www.st.com/internet/com/TECHNICAL_RESOURCES/TECHNICAL_LITERATURE/DATASHEET/CD00169322.pdf
79 | 1 | U8 | PAC1954 | Analog_ADC:PAC1934x-xJQ | Package_DFN_QFN:UQFN-16-1EP_4x4mm_P0.65mm_EP2.7x2.7mm | http://ww1.microchip.com/downloads/en/DeviceDoc/PAC1931-Family-Data-Sheet-DS20005850E.pdf
80 | 1 | U9 | ATtiny1627-M | MCU_Microchip_ATtiny:ATtiny827-M | Package_DFN_QFN:QFN-24-1EP_4x4mm_P0.5mm_EP2.6x2.6mm | https://ww1.microchip.com/downloads/en/DeviceDoc/ATtiny424-426-427-824-826-827-DataSheet-DS40002311A.pdf
81 | 1 | U10 | TXB0108DQSR | Logic_LevelTranslator:TXB0108DQSR | TXB0108:IC_TXB0108RGYR | http://www.ti.com/lit/ds/symlink/txb0108.pdf
82 | 1 | U11 | W25Q16JLSSIG | W25Q:W25Q16JLSSIG | Package_SO:SOIC-8_3.9x4.9mm_P1.27mm
83 | 1 | U12 | RA-02_LORA | RA 02:RA-02_LORA | LORA:MODULE_RA-02_LORA |  | Ai-Thinker | 3.3mm | 2018/03/02 | Manufacturer Recommendations
84 | 1 | U13 | ILD213T | Isolator:LTV-827 | Package_SO:SO-8_5.3x6.2mm_P1.27mm | http://optoelectronics.liteon.com/upload/download/DS-70-96-0016/LTV-8X7%20series%20201610%20.pdf
85 | 2 | U14, U15 | AP62200Z6 | Regulator_Switching:AP62250Z6 | Package_SO:TSOP-6_1.65x3.05mm_P0.95mm | https://www.diodes.com/assets/Datasheets/AP62250.pdf
86 | 3 | U16, U17, U18 | MCP9700AT-ELT | Sensor_Temperature:MCP9700AT-ELT | Package_TO_SOT_SMD:SOT-353_SC-70-5 | http://ww1.microchip.com/downloads/en/DeviceDoc/20001942G.pdf
87 | 1 | Y1 | Crystal_GND24 | Device:Crystal_GND24 | Oscillator:Oscillator_SMD_SeikoEpson_SG210-4Pin_2.5x2.0mm | ~
+ 6 pin 2.54mm magnetic pogo connector

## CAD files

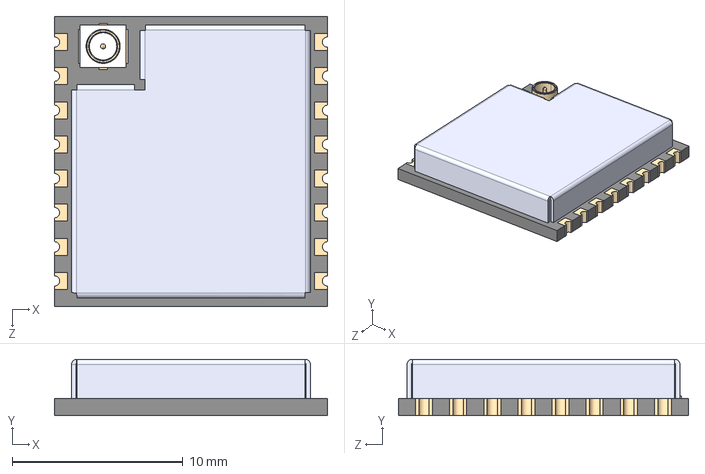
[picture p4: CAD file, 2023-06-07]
PCB/MarvinLib/Ra-02 LoRa--3DModel-STEP-1.STEP
16.0 x 3.30 x 17.0 mm

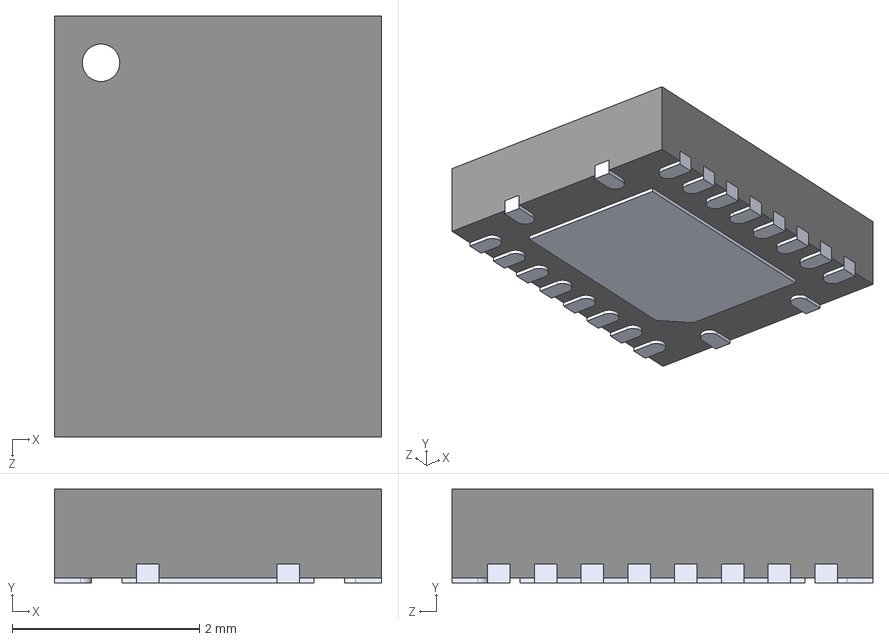
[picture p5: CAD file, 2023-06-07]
PCB/MarvinLib/TXB0108RGYR/TXB0108RGYR.step
3.50 x 1.00 x 4.50 mm

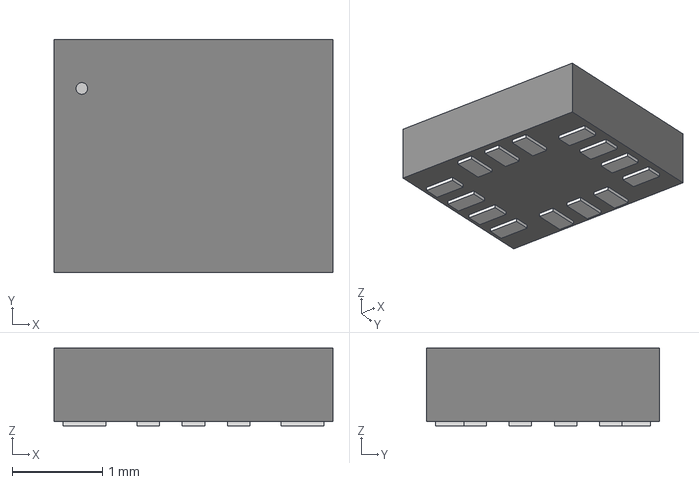
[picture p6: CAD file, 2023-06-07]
PCB/MarvinLib/ul_LSM6DSOTR/2022-09-03_13-29-14/STEP/LGA-14L_2P5X3X0P86_STM.step
3.10 x 2.59 x 0.866 mm

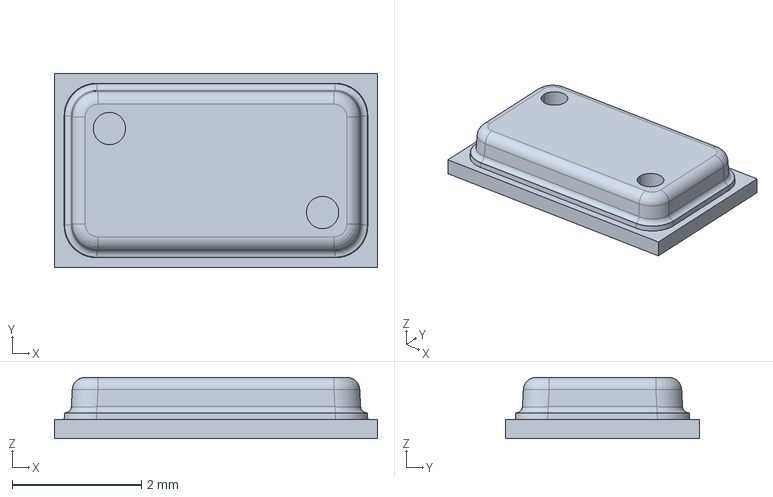
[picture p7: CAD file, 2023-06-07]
PCB/MarvinLib/ul_MS561101BA03-50/STEP/c-ms561101ba03-50-1-3d.stp
5.00 x 3.00 x 0.95 mm

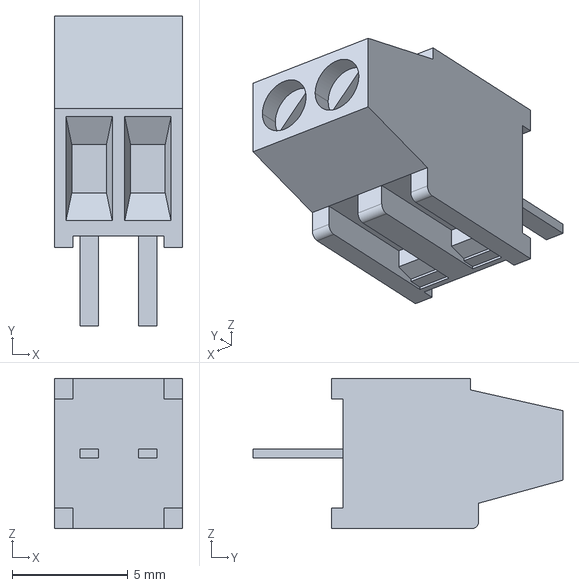
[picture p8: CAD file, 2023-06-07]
PCB/MarvinLib/c-282834-2-c-3d.igs
5.54 x 13.4 x 6.50 mm

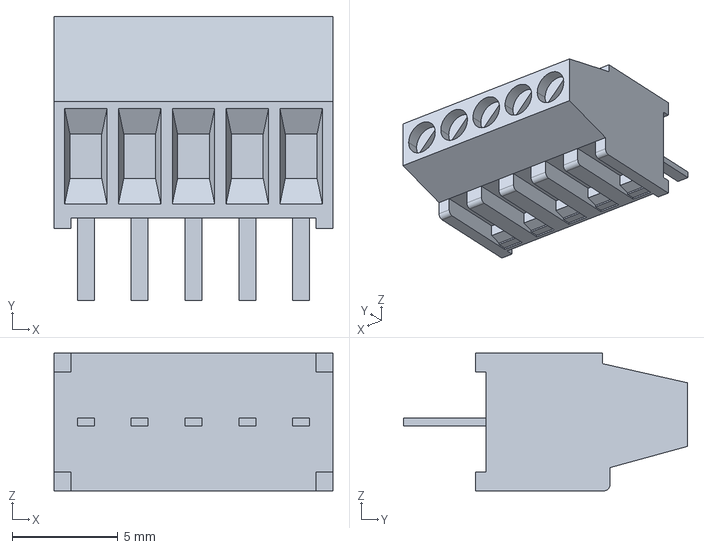
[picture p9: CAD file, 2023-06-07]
PCB/MarvinLib/282834-5--3DModel-STEP-1.STEP
13.2 x 13.4 x 6.50 mm

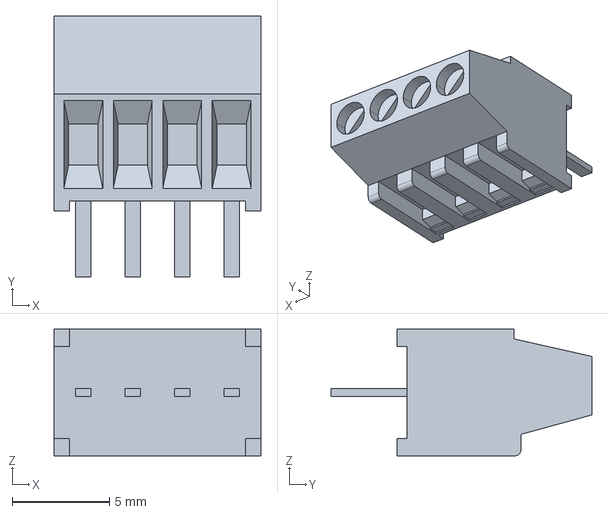
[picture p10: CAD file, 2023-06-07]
PCB/MarvinLib/282834-4--3DModel-STEP-1.STEP
10.6 x 13.4 x 6.50 mm

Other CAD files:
PCB/MarvinLib/ul_LSM6DSRTR/2022-08-28_16-12-26/STEP/LGA-14L_2P5X3X0P83_STM.step
CAD/MarvinP1PCB.f3d

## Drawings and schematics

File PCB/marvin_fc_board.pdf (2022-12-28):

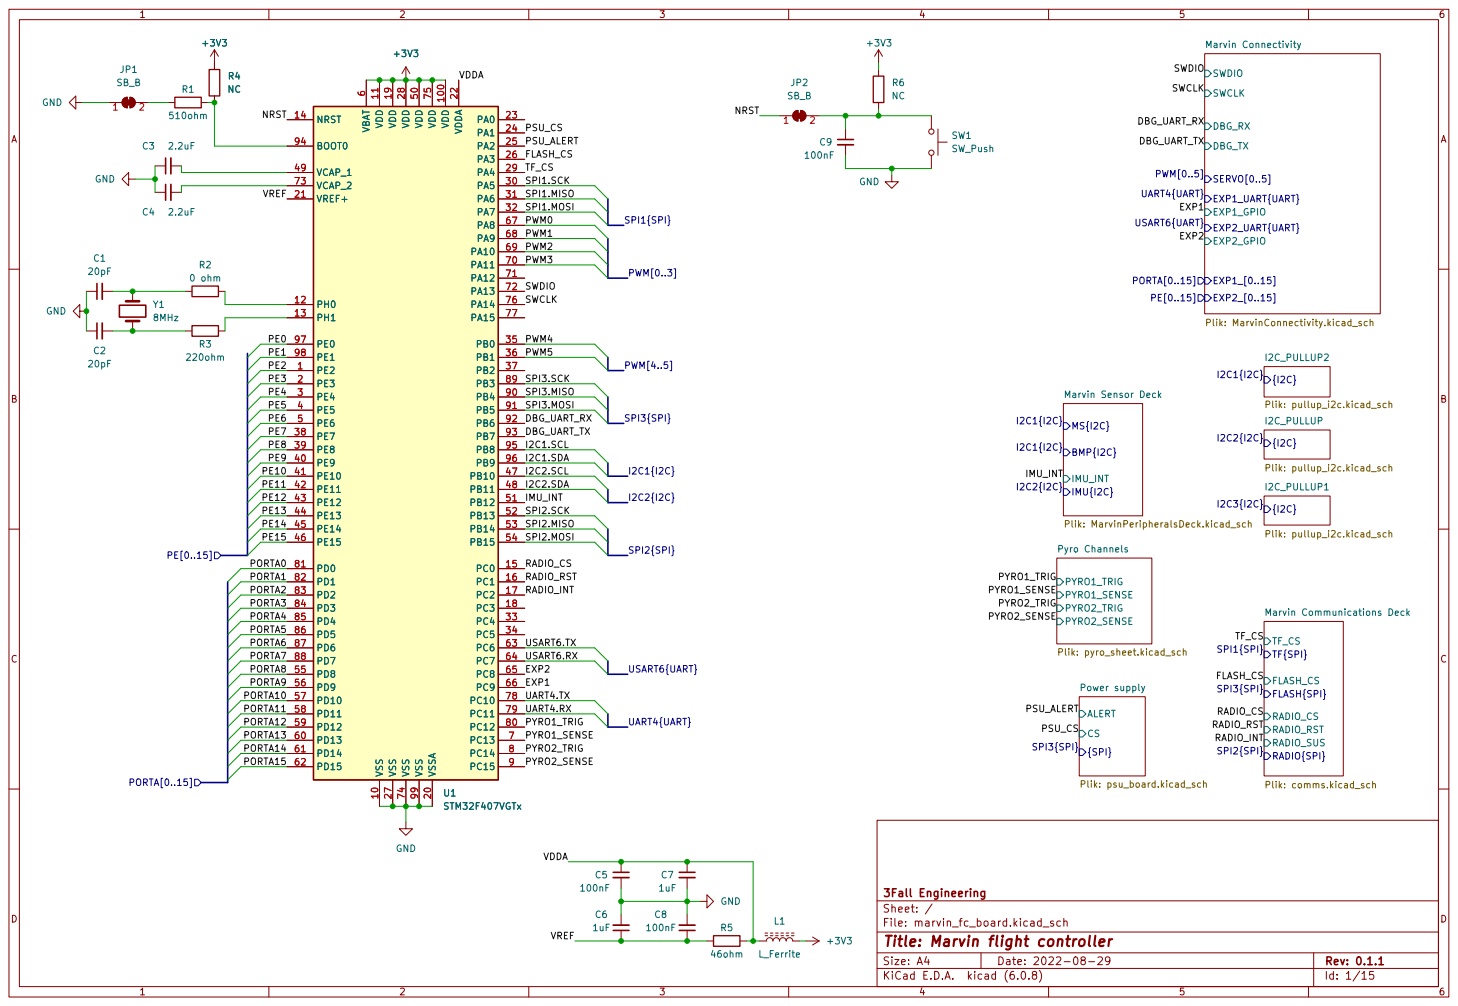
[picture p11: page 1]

BMP{I2C} Marvin Sensor Deck Plik: MarvinPeripheralsDeck.kicad_sch PYRO2_SENSE
I2C1{I2C} PYRO1_TRIG

TF{SPI} Marvin Communications Deck Plik: comms.kicad_sch

{SPI} ALERT Power supply

Id: 1/15 Title: Marvin flight controller

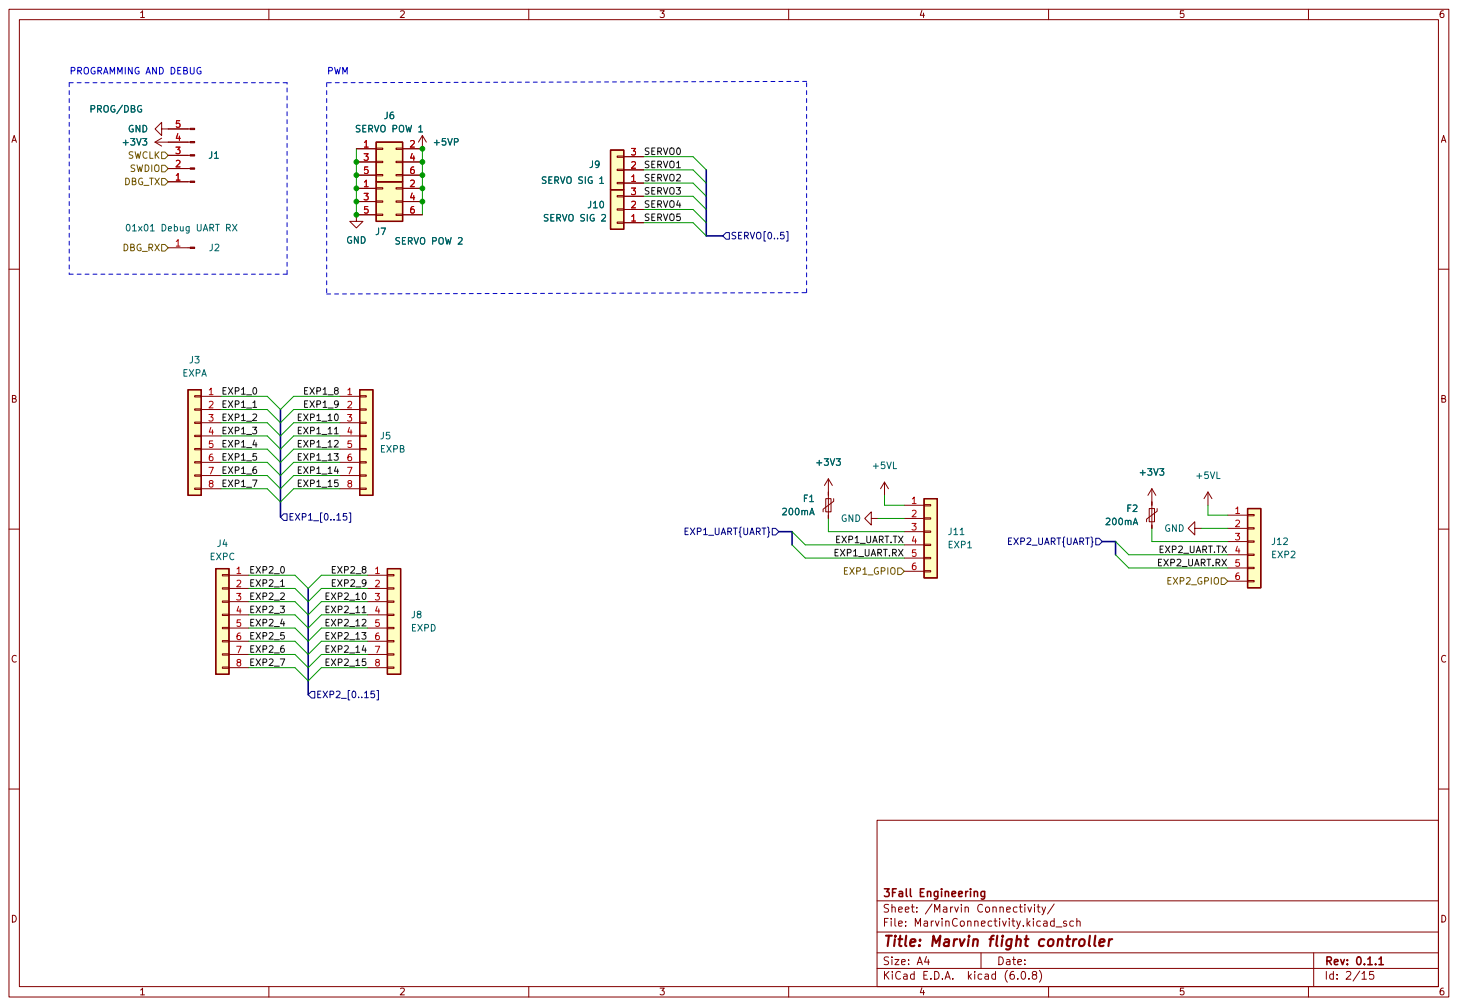
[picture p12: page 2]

5 | J7 SERVO POW 2 +5VP | 6
3 3 | | 4 4

1 1 | | 2 2
5 5 | | 6 6

3Fall Engineering
Sheet: /Marvin Connectivity/
File: MarvinConnectivity.kicad_sch
Id: 2/15 Title: Marvin flight controller

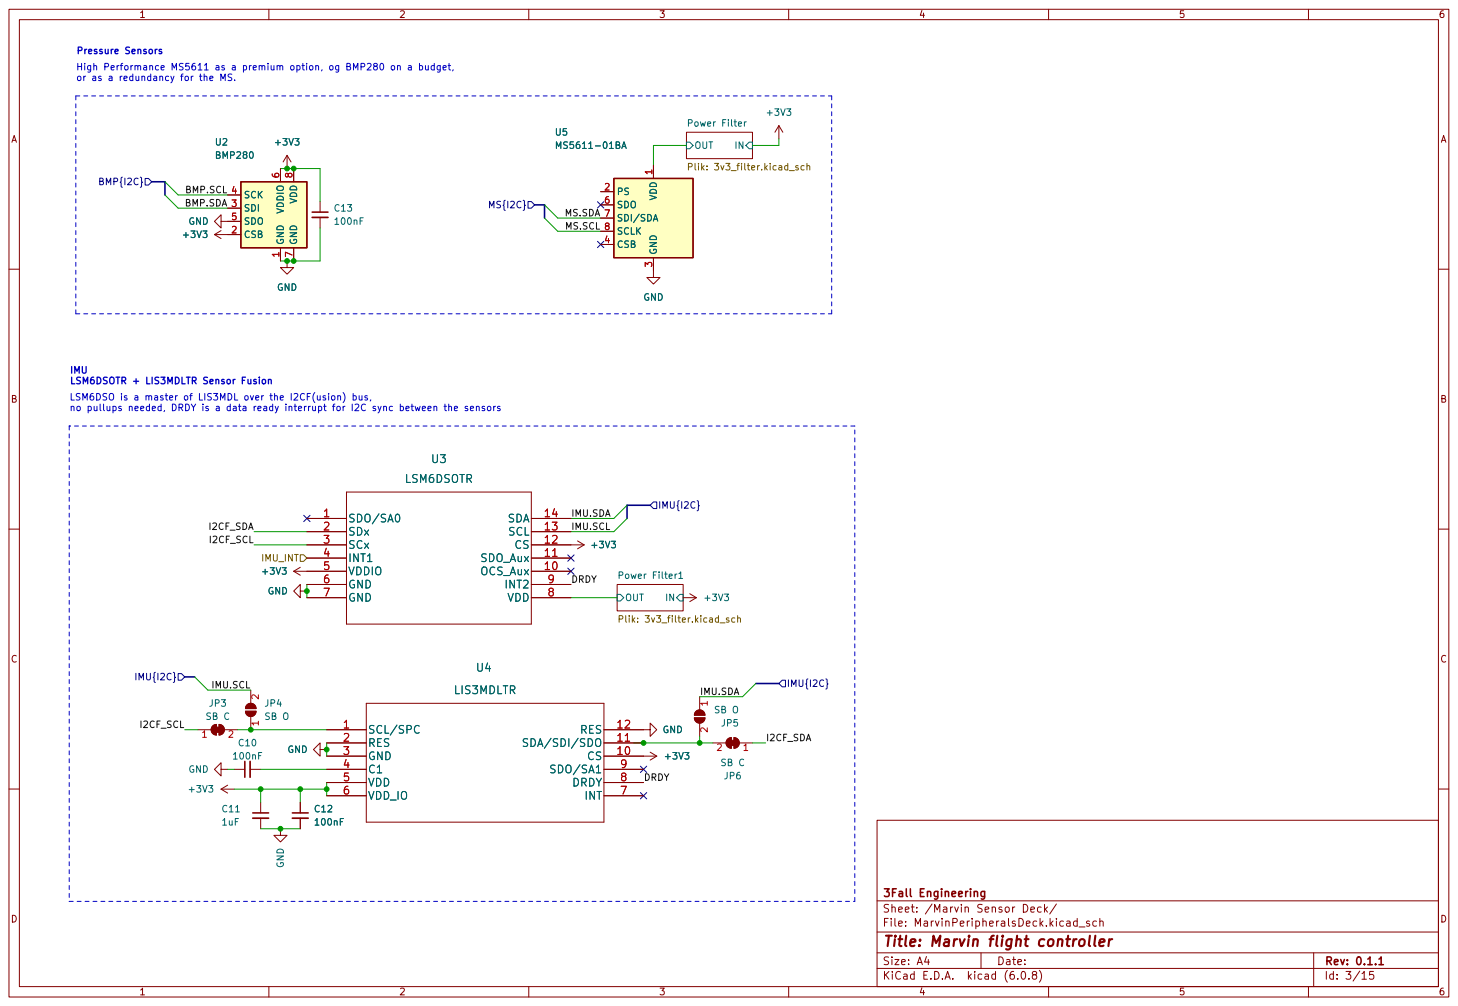
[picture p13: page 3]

IMU LSM6DSOTR + LIS3MDLTR Sensor Fusion High Performance MS5611 as a premium option, og BMP280 on a budget,
I2CF_SCL BMP.SCL
I2CF_SDA MS.SDA
IMU.SDA MS.SCL

3 CSB 4 SDO 6 SDI/SDA 7 SCLK 8 U5MS5611-01BA +3V3 SCL/SPC 1 CS 10 SDA/SDI/SDO 11 RES 12 RES 2 GND 3 C1 4 VDD 5 VDD_IO 6

1 CSB 2 SDI 3 SCK 4 SDO 5 VDDIO

3 CSB 4 SDO 6 SDI/SDA 7 SCLK 8 +3V3 GND

LSM6DSO is a master of LIS3MDL over the I2CF(usion) bus,
no pullups needed, DRDY is a data ready interrupt for I2C sync between the sensors

Id: 3/15 Title: Marvin flight controller

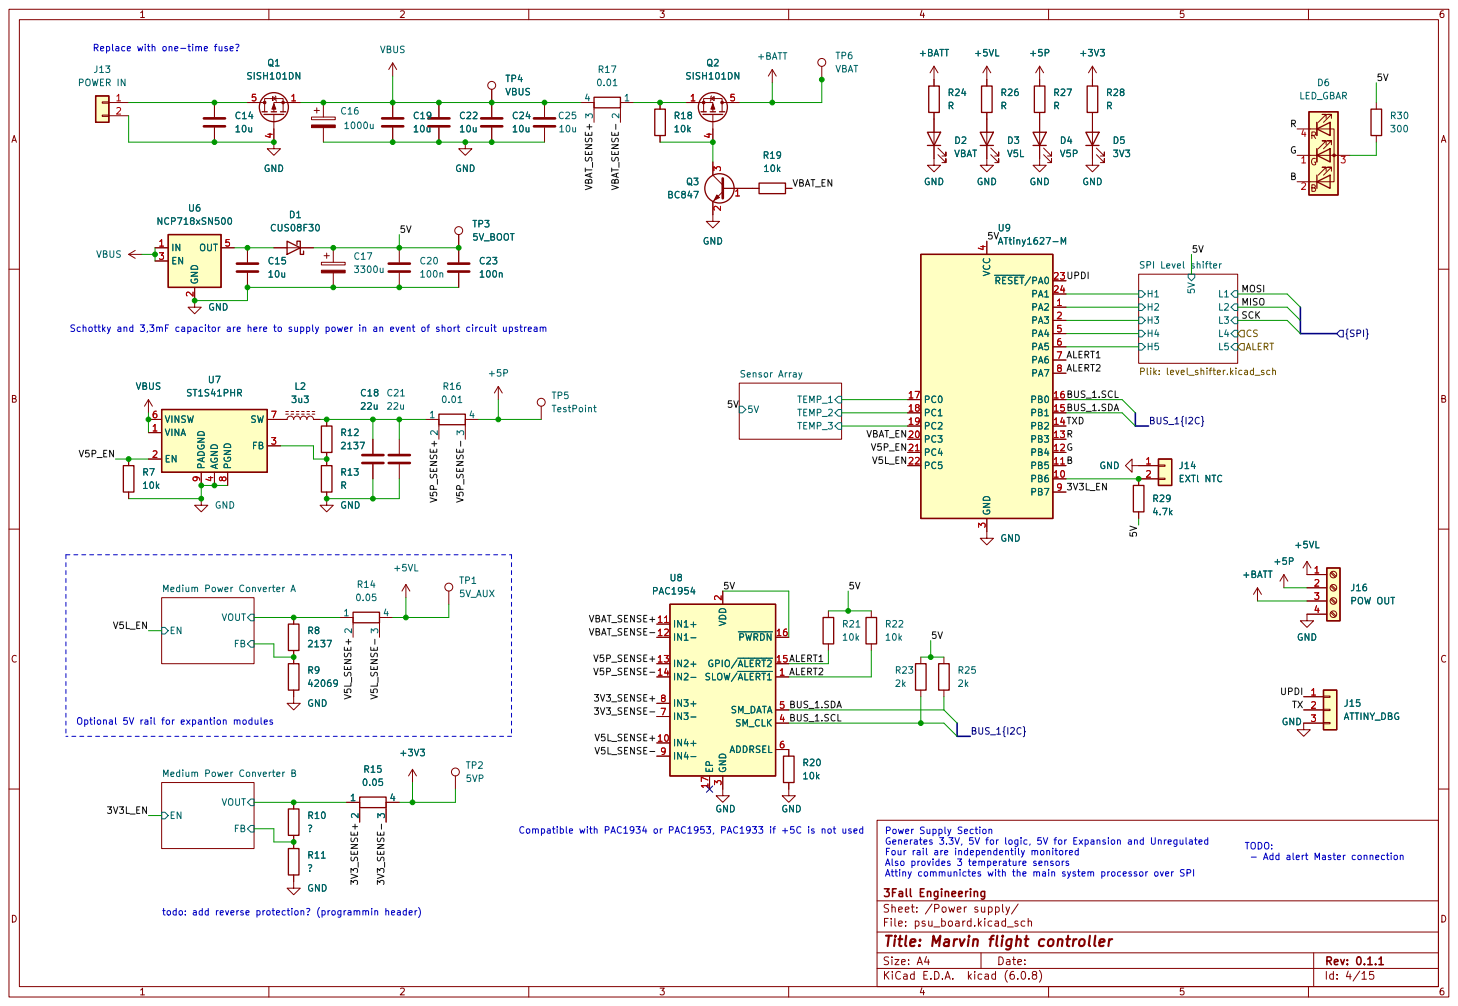
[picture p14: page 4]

Replace with one-time fuse?

Schottky and 3,3mF capacitor are here to supply power in an event of short circuit upstream

ALERT2 Compatible with PAC1934 or PAC1953, PAC1933 if +5C is not used

VOUT Medium Power Converter A

VOUT Medium Power Converter B

Power Supply Section
Generates 3.3V, 5V for logic, 5V for Expansion and Unregulated
Four rail are independentily monitored
Also provides 3 temperature sensors
Attiny communictes with the main system processor over SPI
3Fall Engineering
Sheet: /Power supply/
File: psu_board.kicad_sch
Id: 4/15 Title: Marvin flight controller

- Add alert Master connection

todo: add reverse protection? (programmin header)

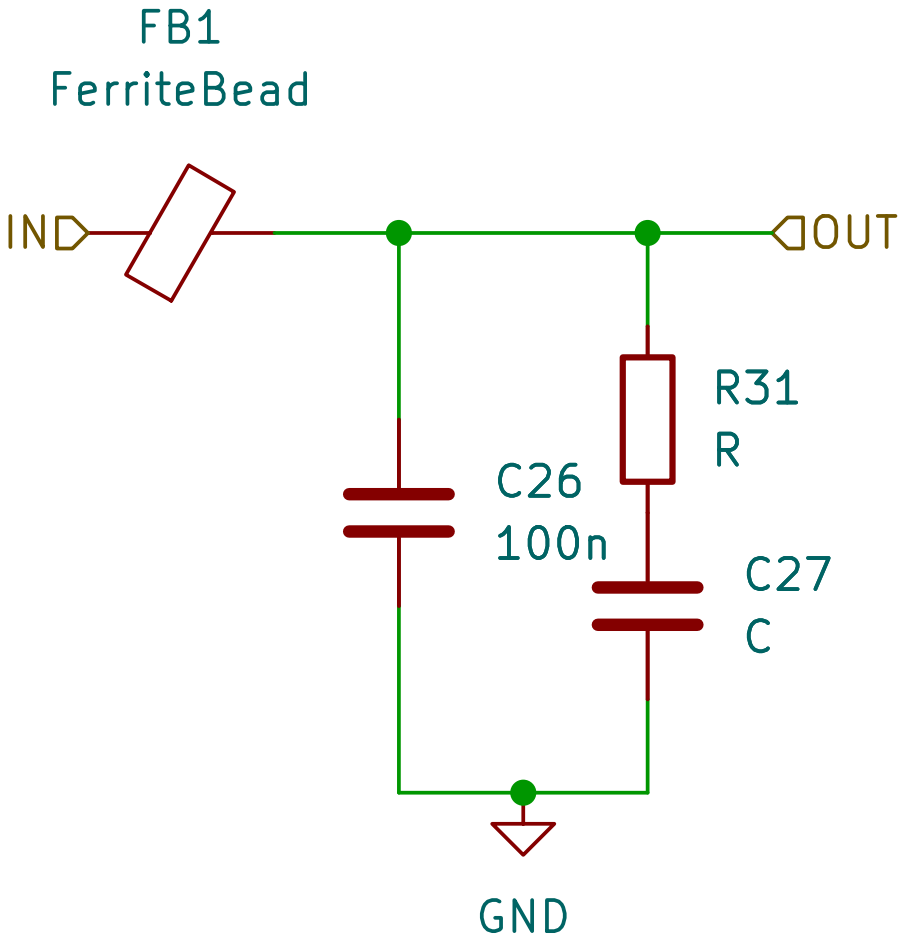
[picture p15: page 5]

File: 3v3_filter.kicad_sch Sheet: /Marvin Sensor Deck/Power Filter1/
Id: 5/15 Title:

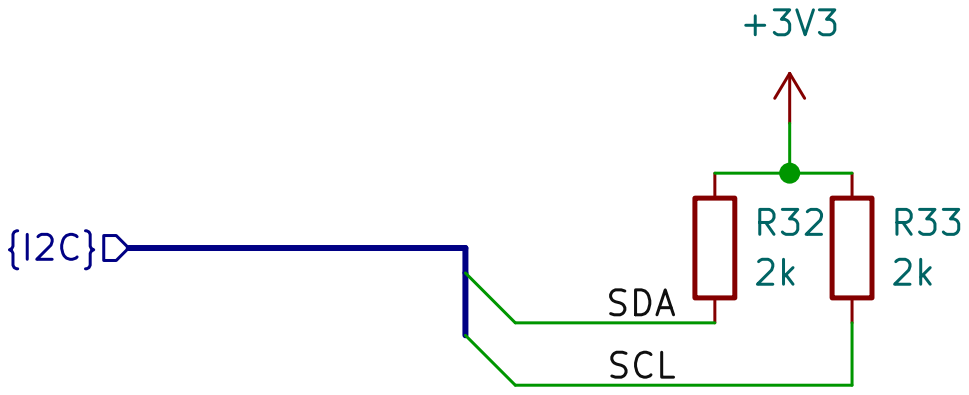
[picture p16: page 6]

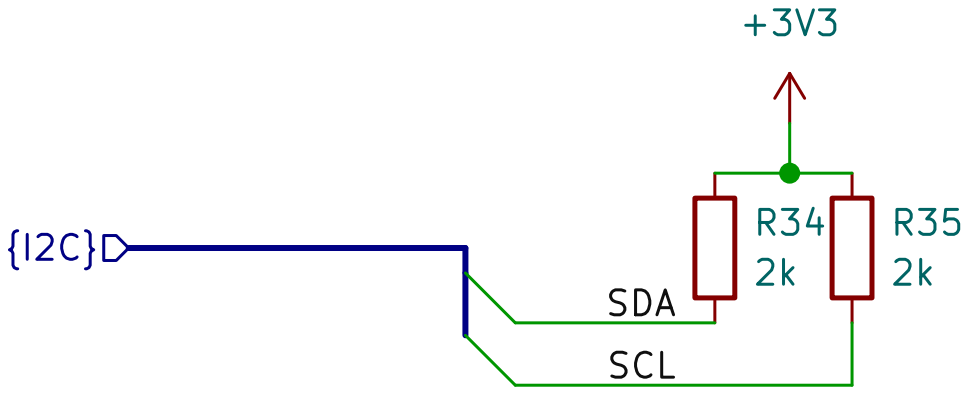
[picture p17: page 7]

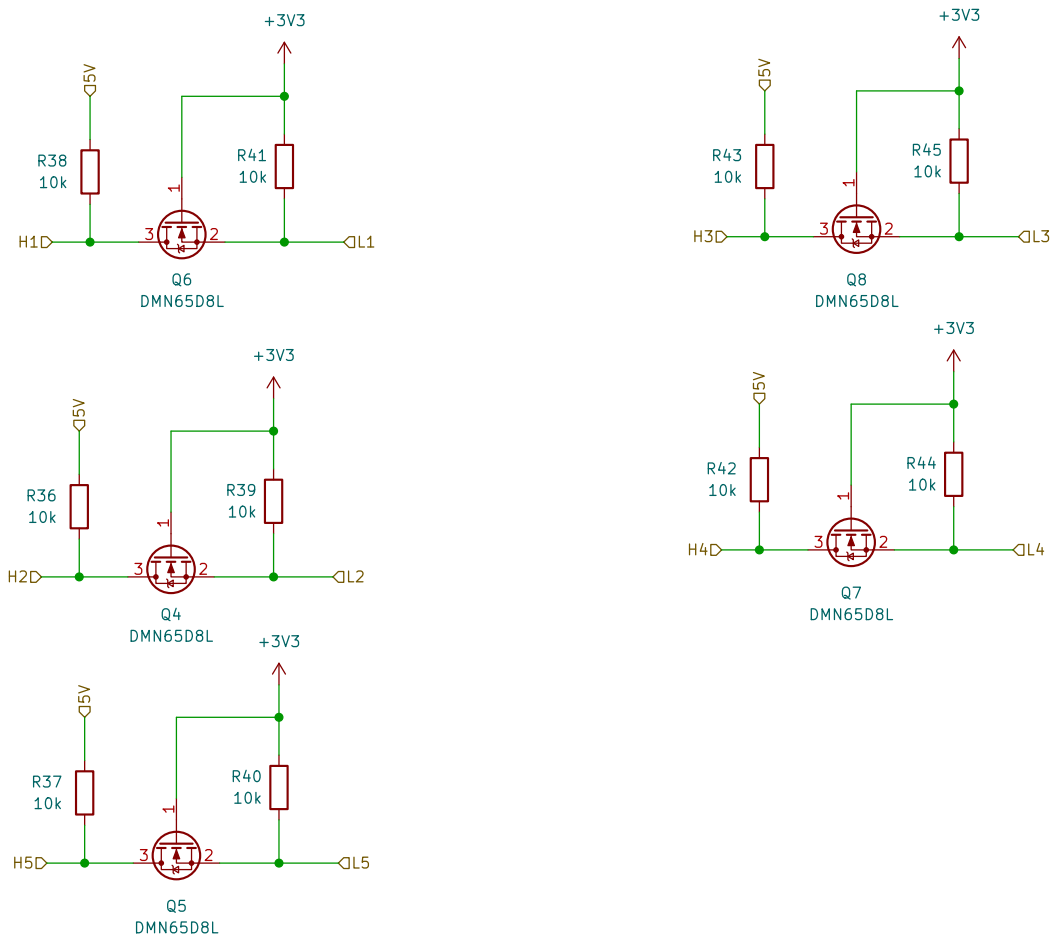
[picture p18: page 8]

3Fall Engineering
Sheet: /Power supply/SPI Level shifter/
File: level_shifter.kicad_sch
Id: 8/15 Title: Marvin flight controller

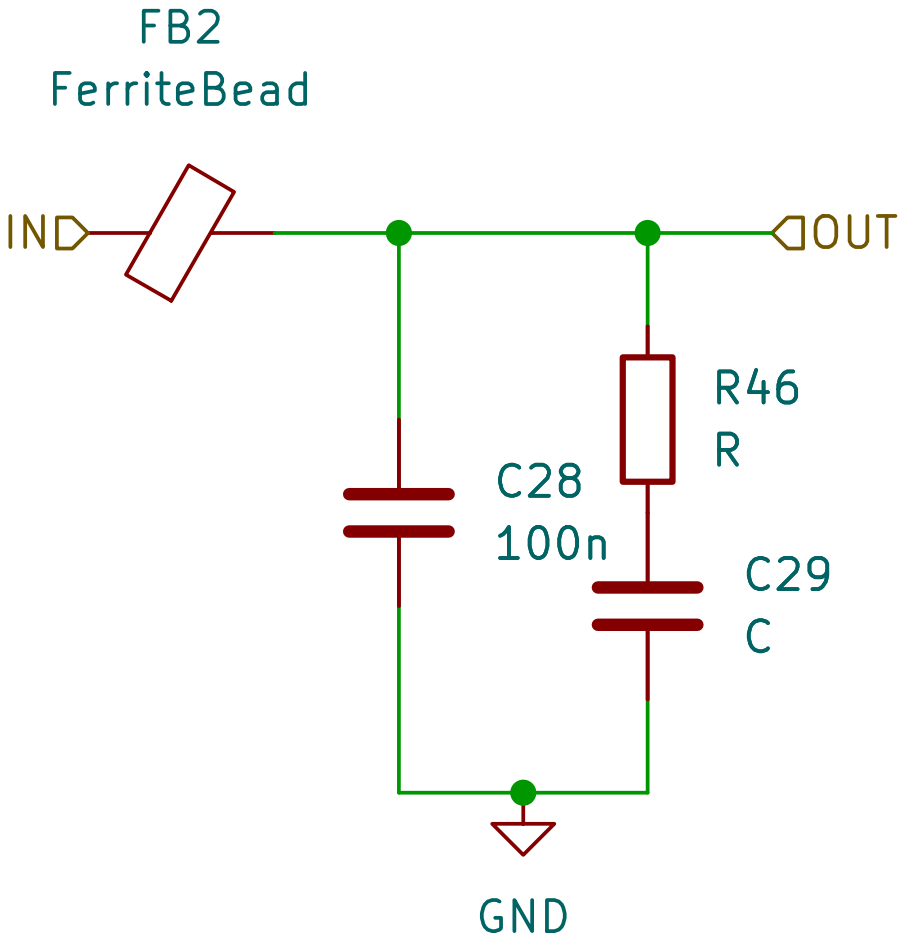
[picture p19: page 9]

File: 3v3_filter.kicad_sch Sheet: /Marvin Sensor Deck/Power Filter/
Id: 9/15 Title:

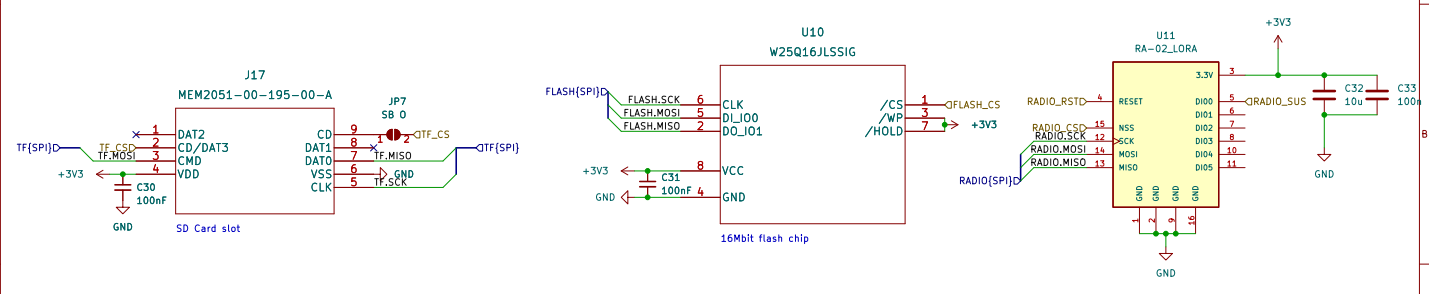
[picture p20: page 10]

1 DI04 10 DI05 11 SCK 12 MISO 13 MOSI 14 NSS 15 GND 16 GND

File: comms.kicad_sch Sheet: /Marvin Communications Deck/
Id: 11/15 Title:

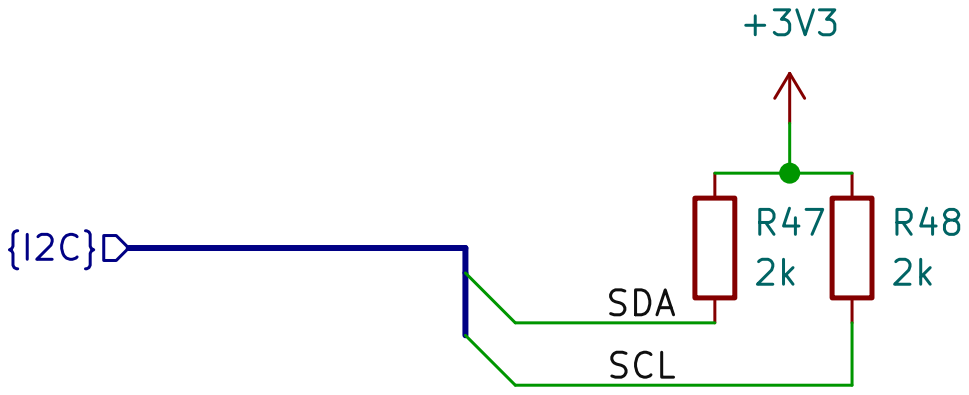
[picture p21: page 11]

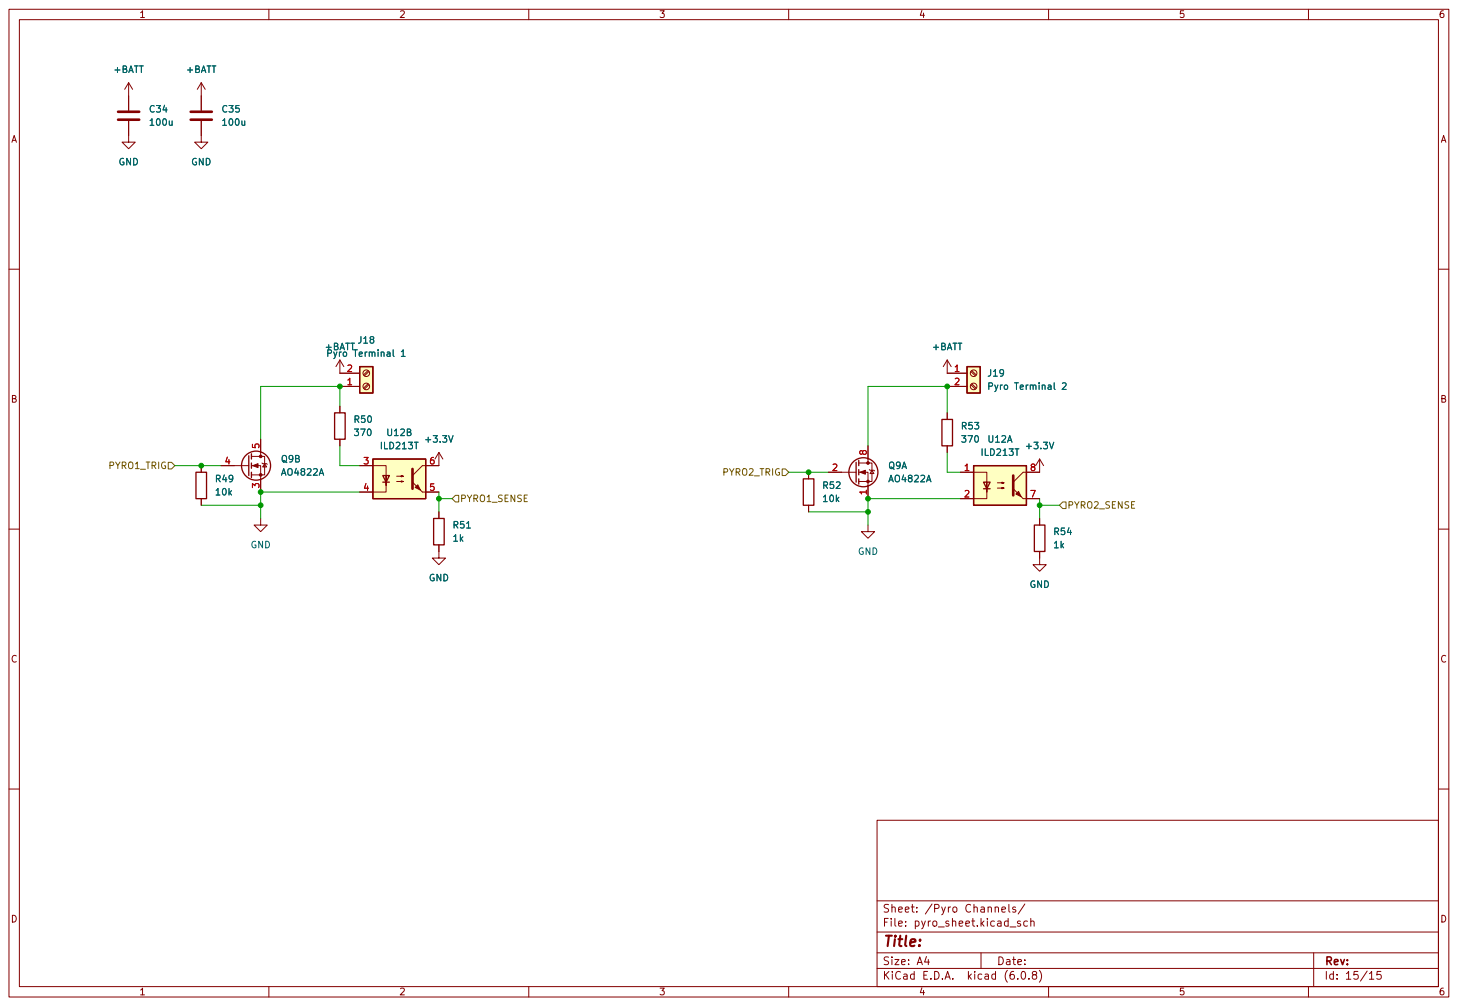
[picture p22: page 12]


3 BST 4 EN 5 FB 6 U13 AP62200Z6 EN FB

Sheet: /Power supply/Medium Power Converter A/
File: medium_power_converter.kicad_sch
Id: #/15 Title: Marvin flight controller


3 BST 4 EN 5 FB 6 U14 AP62200Z6 EN FB

Sheet: /Power supply/Medium Power Converter B/
File: medium_power_converter.kicad_sch
Id: #/15 Title: Marvin flight controller


Sheet: /Power supply/Sensor Array/
File: psu_sensor_array.kicad_sch
Id: #/15 Title: Marvin flight controller
